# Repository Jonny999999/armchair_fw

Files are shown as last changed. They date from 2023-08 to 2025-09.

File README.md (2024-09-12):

# Overview
This repository contains the firmware for a custom-built automated electric armchair.  
Detailed project information and documentation is available on the website:
- ~~V1: [Electric Armchair V1](https://pfusch.zone/electric-armchair)~~
- V2: [Electric Armchair V2](https://pfusch.zone/electric-armchair-v2)

**Note:** In the current version _V2.2_, only the esp-project in the [board_single/](board_single) folder and the custom libraries in [common/](common) are used.  
The projects in the folders `board_control/` and `board_motorctl/` are no longer compatible and are legacy from _V2.1_.

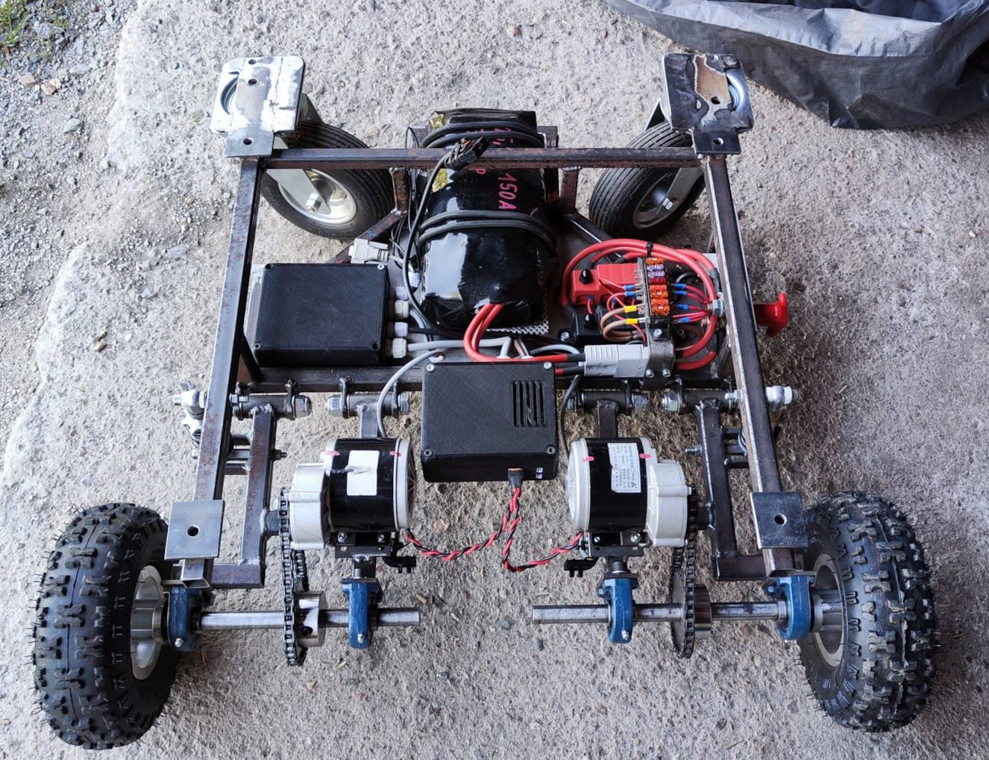
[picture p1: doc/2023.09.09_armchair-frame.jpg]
Photo machine
<br>
*Photo of the built frame that carries the armchair*

<br>

## Current Features
- **Control Modes:**
  - **Joystick:** Control movement via hardware joystick mounted on the right armrest
  - **HTTP:** Control movement via virtual joystick on a web interface
  - **Massage:** Armchair shaking depending on stick position
  - **Adjust:** Control leg and backrest position via joystick
  - **Auto:** Execute stored driving commands sequentially
- **Advanced Motor Control:**
  - Deceleration limit
  - Acceleration limit
  - Current limit
  - Braking
  - Compatible with different motor drivers:
    - 3 pins: A, B, PWM - e.g. various common H-Bridges
    - 1 pin: UART/RS232 - e.g. Sabertooth
- **Input/Sensors:**
  - **Speed Measurement:** Measures speed and direction of each tire individually using custom built encoders
  - **Current Measurement:** Monitors current of each motor
  - **Battery Voltage:** Measures battery voltage and calculates percentage according to discharge curve
  - **Analog Joystick:** 
    - Evaluate two analog signals to get coordinates, radius and angle
    - Calibration wizard/sequence
    - Calibration stored persistently in nvs
- **Fan Control:** Cooling fan for motor driver are activated when needed only
- **Buzzer:** Provides acoustic feedback when switching modes or interacting with menu
- **OLED-Display + Rotary-encoder:**
  - Various status screens showing battery status, speed, RPM, motor current, mode, power, duty cycle, stick data
  - Menu for setting various options using encoder
  - Changed settings are stored persistently in NVS flash
  - Menu for selecting the control mode
- **UART Communication between 2 Boards (V2.1)**
- **Electric Chair Adjustment:** Control 4 Relays powering motors that adjust the chair rest positions
- **Wi-Fi:**
  - Hosts wireless network
  - Web server with webroot in SPIFFS
  - HTTP API for controlling the chair (remote control)
- **React web-app:** Virtual joystick sending data to http-API (placed in SPIFFS)

## Planned Features
#### Hardware
- More Sensors:
  - Accelerometer
  - Lidar sensor / collision detection
  - GPS receiver
  - Temperature sensors
- Lights
- Camera
#### Algorithms
- Anti-Slip Regulation
- Self-Driving Algorithm
#### UI
- Improved Web Interface
  - Settings
  - Chair adjustment
- Simple App

<br>

## Hardware Setup / Electrical
### Control-PCB
The firmware is designed for an ESP32 microcontroller integrated into a custom PCB developed here: [Project Work 2020](https://pfusch.zone/project-work-2020)

### Connection Plan
A detailed diagram illustrating all components and wiring can be found in the file [connection-plan.drawio.pdf](connection-plan.drawio.pdf).   
For more details refer to the documentation on the [website](https://pfusch.zone/electric-armchair-v2).

### Chair-Adjust Relay-Board
A custom pcb with relays and protection for controlling the 2 motors that adjust the rest positions of the armchair was created in this repository as well:
Date: 2024.09.08  
Folder: [hardware/chairAdjust-relayBoard](hardware/chairAdjust-relayBoard)  
Schematic: [hardware/chairAdjust-relayBoard/export/schematic.pdf](hardware/chairAdjust-relayBoard/export/schematic.pdf)
<br>
<br>
<p align="center">

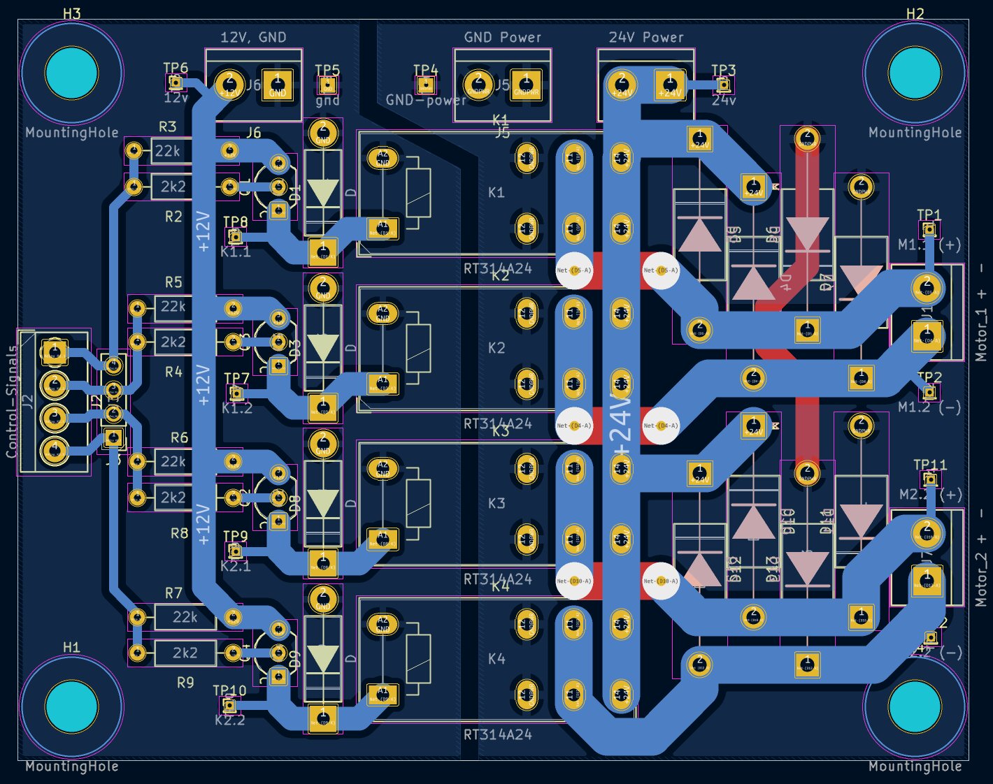
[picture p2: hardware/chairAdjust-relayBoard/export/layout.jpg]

</p>

<br>
<br>

# Installation
### Install ESP-IDF
For this project **ESP-IDF v4.4.4** is required
```bash
#download esp-idf
yay -S esp-idf #alternatively clone the esp-idf repository from github
#run installation script in installed folder
/opt/esp-idf/install.sh
```
### Clone Repository
```
git clone git@github.com:Jonny999999/armchair_fw
```
### Install Node Packages
Navigate to the react-app directory and install required packages using npm:
```
cd react-app
npm install
```

<br>
<br>

# Building the Project
## React-webapp
When flashing to the ESP32, the files in the `react-app/build/` folder are written to a SPIFFS partition.  
These files are then served via HTTP in the Wi-Fi network "armchair" created by the ESP32.  

Initially, or when changing the React code, you need to manually build the React app:
```bash
cd react-app
#compile
npm run build
#remove unwanted license file (filename too long for spiffs)
rm build/static/js/main.8f9aec76.js.LICENSE.txt
```
**Note:** For testing the app locally, use `npm start`

## Firmware
### Environment Setup
```bash
source /opt/esp-idf/export.sh
```
Run once per terminal

### Compilation
```bash
cd board_single
idf.py build
```

### Upload
- Connect FTDI programmer to board (GND to GND, TX to RX, RX to TX)
- Press RESET and BOOT button
- Release RESET button (keep pressing boot)
- Release boot button
- Run flash command:
```bash
idf.py flash
```

### Monitor
To view log output for debugging, follow the same steps as in the Upload section, but run:
```bash
idf.py monitor
```

<br>
<br>

# Usage / User Interface

## Quickstart
- **Browse / select any mode**
  - `[long press]` opens menu for selecting the desired mode (*JOYSTICK* for driving)
- **Driving**
  - `[3x click]` enters *JOYSTICK* mode
- **Rest position**
  - `[rotate]` adjusts the leg rest position  
  - `[press + rotate]` at the same time: adjusts the back rest position
  - alternatively enter *ADJUST* mode and control rests via joystick

<br>

## Encoder Functions
- *When not in MENU mode*, **rotating the encoder** has the following functions:

| Encoder Event | Action |
|---|---|
| rotate left | Move leg rest up by 10% |
| rotate right | Move leg rest DOWN by 10% |
| press + rotate left | Move back rest down by 5% |
| press + rotate left | Move back rest up by 5% |

Note: first tick is ignored -> quickly rotate 2 ticks at first

<br>

- *When not in MENU mode*, **clicking the encoder** has the following functions:

| Count | Type | Action | Description |
|---|---|---|---|
| 1x long | switch mode | **MENU_MODE_SELECT** | Open **menu for selecting the current control mode** |
| 1x | control | [MASSAGE] **freeze** input  | When in massage mode: lock or unlock joystick input at current position. |
| 1x short, 1x long | switch mode | **ADJUST-CHAIR**  | Switch to mode where the armchair leg and backrest are controlled via joystick. |
| 2x | toggle mode | **IDLE** <=> previous| Enable/disable chair armchair (e.g., enable after startup or switch to previous mode after timeout). |
| 3x | switch mode | **JOYSTICK** | Switch to JOYSTICK mode, to control armchair using joystick (default). |
| 4x | switch mode | **HTTP** | Switch to **remote control** via web-app `http://191.168.4.1` in wifi `armchair`. |
| 5x | switch mode | **MENU_SETTINGS** | Open menu to set various options, controlled via display and rotary encoder. |
| 6x | switch mode | **MASSAGE** | Switch to MASSAGE mode where armchair shakes differently, depending on joystick position. |
| 7x | | | |
| 8x | toggle option| **deceleration limit** | Disable/enable deceleration limit (default on) => more responsive. |
| 12x | toggle option| **alt stick mapping** | Toggle between default and alternative stick mapping (reverse direction swapped). |

<br>

- When in **MENU_SETTINGS mode** (5x click), the encoder controls the settings menu: (similar in MENU_MODE_SELECT)

| Encoder Event | Current Menu | Action |
|---|---|---|
| long press | main-menu | Exit MENU mode to previous control mode (e.g., JOYSTICK). |
| long press | value-select | Exit to main-menu without changing the value. |
| click | main-menu | Select currently highlighted menu item -> enter value-select screen. |
| click | value-select | Confirm value / run action. |
| rotate | main-menu | Scroll through menu items. |
| rotate | value-select | Change value. |

<br>

## HTTP Mode
Control the armchair via a virtual joystick on the web interface.

**Usage:**
- Switch to HTTP mode (4 button presses or via mode-select menu).
- Connect to WiFi `armchair`, no password.
- Access http://192.168.4.1 (note: **http** NOT https, some browsers automatically add https!).

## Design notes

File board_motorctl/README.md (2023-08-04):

Firmware for a homemade automated electric armchair.  
More details about this project: https://pfusch.zone/electric-armchair

# Installation
### Install esp-idf
For this project **ESP-IDF v4.4.4** is required (with other versions it might not compile)
```bash
#download esp-idf
yay -S esp-idf #alternatively clone the esp-idf repository from github
#run installation script in installed folder
/opt/esp-idf/install.sh
```
### Clone this repo
```
git clone git@github.com:Jonny999999/armchair_fw
```
### Instal node packages
For the react app packages have to be installed with npm TODO: add this to cmake?
```
cd react-app
npm install
```

# Compilation
## react-webapp
For the webapp to work on the esp32 it has to be built.
When flashing, the folder react-app/build is flashed to siffs (which is used as webroot) onto the esp32.
The following command builds the react webapp and creates this folder
TODO: add this to flash target with cmake?
```bash
cd react-app
#compile
npm run build
#remove unwanted license file (filename too long for spiffs)
rm build/static/js/main.8f9aec76.js.LICENSE.txt
```
Note: Use `npm start` for starting the webapp locally for testing

## esp project
### Set up environment
```bash
source /opt/esp-idf/export.sh
```
(run once in terminal)

### Compile
```bash
idf.py build
```

### Upload
- connect FTDI programmer to board (VCC to VCC; TX to RX; RX to TX)
- press REST and BOOT button
- release RESET button (keep pressing boot)
- run flash command:
```bash
idf.py flash
```
- once "connecting...' successfully, BOOT button can be released

### Monitor
- connect FTDI programmer to board (VCC to VCC; TX to RX; RX to TX)
- press REST and BOOT button
- release RESET button (keep pressing boot)
- run monitor command:
```bash
idf.py monitor
```
- once connected release BOOT button
- press RESET button once for restart

# Hardware setup
## pcb
Used pcb developed in this project: https://pfusch.zone/project-work-2020

## connection plan
A diagram which shows what components are connected to which terminals of the pcb exists here:  
[connection-plan.drawio.pdf](connection-plan.drawio.pdf)

# Planned Features
- More sensors:
  - Accelerometer
  - Lidar sensor
  - GPS receiver
- Anti slip regulation
- Self driving algorithm
- Lights
- drinks holder
- improved webinterface

# Todo
**Add switch functions**
- set loglevel
- define max-speed
- calibrate joystick (min, max, center)
- testing mode / dry-run

# Usage
## Switch functions
**Currently implemented**
| Count | Type | Action | Description |
| --- | --- | --- | --- |
| 1x | configure | [JOYSTICK] **calibrate stick** | when in joystick mode: set joystick center to current joystick pos |
| 1x | control | [MASSAGE] **freeze** input | when in massage mode: lock or unlock joystick input at current position |
| 2x | toggle mode | **IDLE** <=> previous | enable/disable chair armchair e.g. enable after startup or timeout |
| 3x | switch mode | **JOYSTICK** | switch to default mode JOYSTICK |
| 4x | toggle mode | **HTTP** <=> JOYSTICK | switch to '**remote control** via web-app `http://191.168.4.1`' or back to JOYSTICK mode |
| 5x | | | |
| 6x | toggle mode | **MASSAGE** <=> JOYSTICK | switch to MASSAGE mode or back to JOYSTICK mode |
| 7x | | | |
| 8x | toggle option | **deceleration limit** | disable/enable deceleration limit (default on) => more responsive |
| | | | |
| 12x | toggle option | **alt stick mapping** | toggle between default and alternative stick mapping (reverse swapped) |
| >1s | system | **restart** | Restart the controller when pressing the button longer than 1 second | 
| 1x short, 1x long | auto command | **eject** foot support | automatically go forward and reverse for certain time with no acceleration limits, so foot support ejects |

## HTTP mode
Control armchair via virtual joystick on a webinterface.  

**Usage**
- Connect to wifi `armchar`, no password
- Access http://192.168.4.1  (note: **http** NOT https, some browsers automatically add https!)  

**Current Features**
- Control direction and speed with joystick  

**Todo**
- Set parameters
- Control other modes
- Execute preset movement commands

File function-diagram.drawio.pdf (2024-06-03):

# joystick mapping

## Turn right

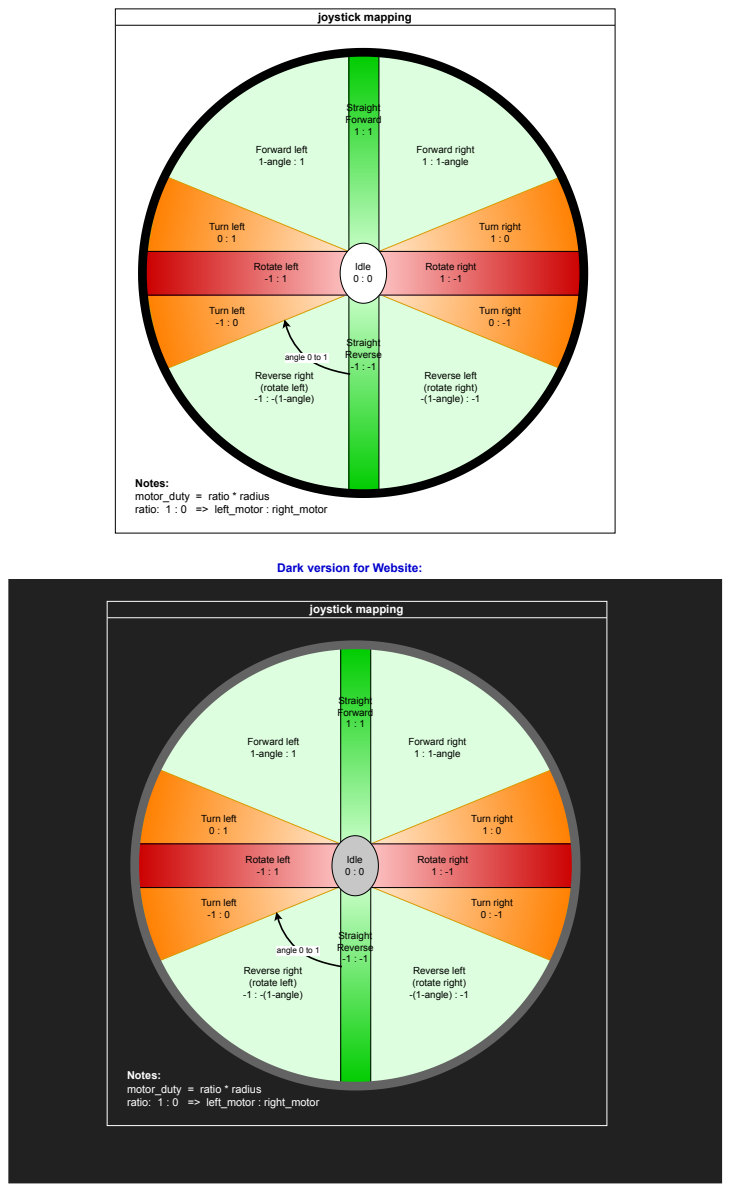
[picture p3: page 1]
Turn left 0 : 1; Rotate left -1 : 1; Rotate right 1 : -1; Straight Reverse -1 : -1; Straight Forward 1 : 1; Forward left 1-angle : 1; Forward right 1 : 1-angle; Reverse right (rotate left) -1 : -(1-angle); Reverse left (rotate right) -(1-angle) : -1; angle 0 to 1; Turn right 0 : -1; Turn left -1 : 0; Idle 0 : 0; Notes: motor_duty = ratio * radius ratio: 1 : 0 => left_motor : right_motor; joystick mapping; Turn right 1 : 0

Dark version for Website:

UART board communication (V2.1)

MOTOR COMMANDS
[ interval, fast ]

timestamp
motorcommands
- motorCommand_t left
- motorstate
- duty

CONFIG
[ manual / on change ]

timestamp
motorctl_config_t
- msFadeAccel
- msFadeDecel
- bool currentLimitEnabled
- (currentSensor_adc)
(currentSensor_ratedCurrent)
- currentMax
- deadTimeMs

board control

- joystick
- encoder, switch
- display

board motorctl

- 2x driver
- 2x currentsensor
- 2x light barrier axle speed
- 2x brake resistor
- temp sensors
- motor
- driver
- brake resistor
- fan

MOTORCTL_STATUS
[ interval, slow ]

timestamp
motorcommands (current actual duty, direction) motor currents
axle rotating speed
temperatures
- motors
- drivers
- brake resistors
fan target state [ ] handled by motorctl board battery voltage
config?

## UART

Planning data / structs
need to be sent between the two boards here:

NOTE: the below diagrams are significantly outdated -- needs update to match the actual code again

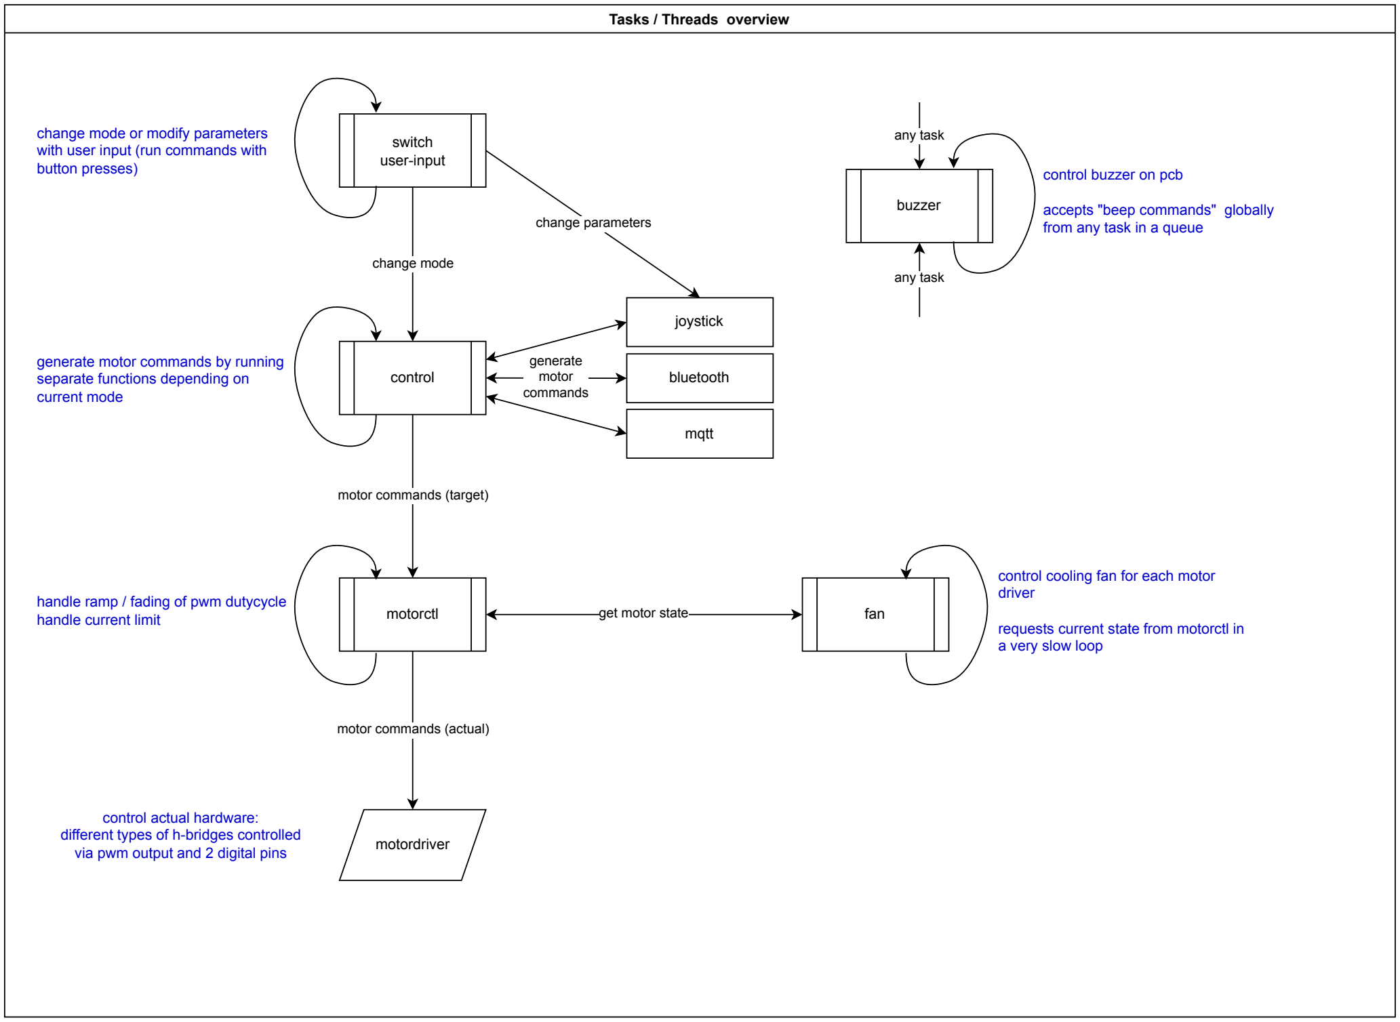
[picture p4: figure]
Tasks / Threads overview; motordriver; joystick; motor commands (actual); motorctl; switch user-input; motor commands (target); control; bluetooth; control actual hardware: different types of h-bridges controlled via pwm output and 2 digital pins; handle ramp / fading of pwm dutycycle handle current limit; generate motor commands by running separate functions depending on current mode; change mode or modify parameters with user input (run commands with button presses); change mode; generate motor commands; mqtt; get motor state; fan; control cooling fan for each motor driver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
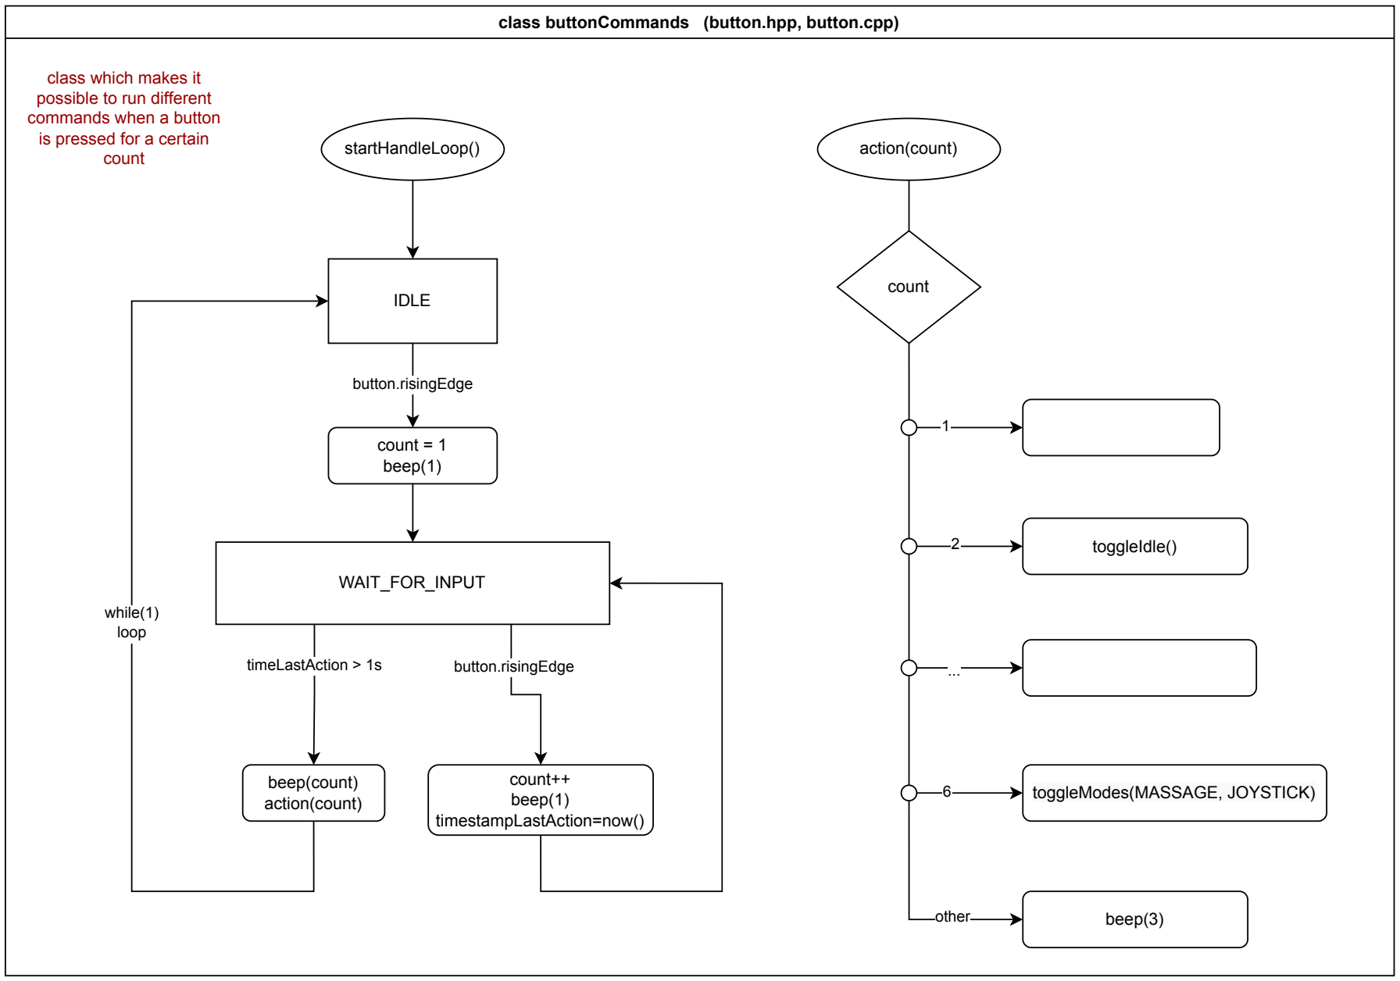
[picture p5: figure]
class buttonCommands (button.hpp, button.cpp); WAIT_FOR_INPUT; count++ beep(1) timestampLastAction=now(); button.risingEdge; IDLE; count = 1 beep(1); count; toggleIdle(); while(1) loop; beep(count) action(count); timeLastAction > 1s; beep(3); toggleModes(MASSAGE, JOYSTICK); other; startHandleLoop(); action(count); class which makes it possible to run different commands when a button is pressed for a certain count

class controledArmchair (control.hpp, control.cpp)

mode:
JOYSTICK

mode:
MQTT

mode:
IDLE

commands =
joystick_generateCmdsDrive(joystick) | while(1) loop

motorLeft.setTarget(command.left.state, command.left.duty) motorRight.setTarget(command.right.state, command.right.duty) commands.right = {IDLE, 0}
commands.left = {IDLE, 0} | Queue_receive (mqttQueue, &command)

changeMode(modeNew)

mode

startHandleLoopl()

MQTT
timeout?

mode:
MASSAGE

commands =
joystick_generateCmdsMassage(joystick)

mode:
BLUETOOTH?

mode:
AUTO?

generate motor
commands by calling
functions
corresponding to
current mode

send target state and duty to controlledMotor object of each motor (controlledMotor applies ramp and current limit and commands motor driver repeatedly)

TODO: timeout
switch to idle when no
change over long time

TODO: add option
"debug / disable motors / dry-run": run the functions to generate the commands and outputs them, but do not send to motor control

run functions corresponding to the current mode that generate motor commands,

send the resulting commands to motorctl

mode = modeNew;

toggleIdle() | toggleModes(modePrimary, modeSecondary)
mode | IDLE | mode = modePrevious

modePrevious = mode
mode = IDLE

[other]

mode | modePrimary | mode = modeSecondary

mode = modePrimary

[other]

toggle between IDLE and
previous or default mode switch to specific mode toggle between two specific modes e.g. button press switches between MASSAGE and JOYSTICK

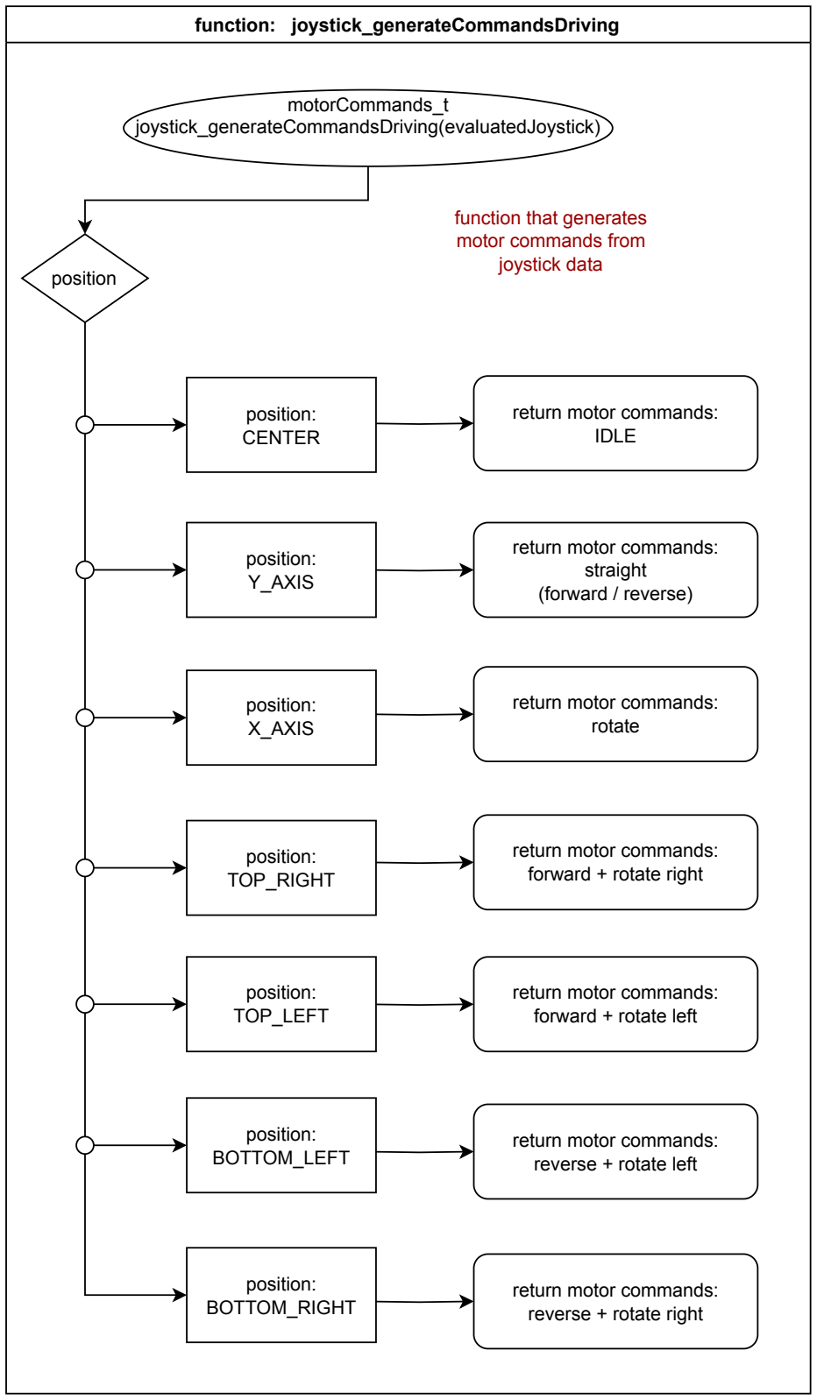
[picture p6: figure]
function: joystick_generateCommandsDriving; motorCommands_t joystick_generateCommandsDriving(evaluatedJoystick); return motor commands: IDLE; return motor commands: straight (forward / reverse); return motor commands: rotate; return motor commands: forward + rotate right; return motor commands: forward + rotate left; return motor commands: reverse + rotate left; return motor commands: reverse + rotate right; position: CENTER; position: Y_AXIS; position: X_AXIS; position: TOP_RIGHT; position: TOP_LEFT; position: BOTTOM_LEFT; position: BOTTOM_RIGHT; position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

class evaluatedJoystick (joystick.hpp, joystick.cpp)

defineCenter()

float getCooridnate(gpio, min, max, center, tolerance)

voltage
> max - tolerance

voltage
< min + tolerance

else

else

voltage < center +
tolerance
&& voltage > center -
tolerance

return 0

return 1

return -1

center

max

min

voltage
> center

else

voltage
< center

else

positive area
(above center)

negative area
(below center)

range = max - center - 2* tolerance return (voltage - center - tolerance) / range

range = center - min - 2* tolerance return - (center - voltage - tolerance) / range x = getCoordinates (gpio_x, min, max, center, tolerance) y = getCoordinates (gpio_y, min, max, center, tolerance)

voltage = read_adc(gpio)

radius = sqrt(pow(joystick.x,2) + pow(joystick.y,2));

angle = (atan(joystick.y/joystick.x) * 180) / 3.141

struct getData()

define state "position" enum
[ CENTER, Y_AXIS, X_AXIS, TOP_RIGHT, TOP_LEFT, BOTTOM_LEFT, BOTTOM_RIGHT ]

x_center = read_adc(gpio_x) y_center = read_adc(gpio_y)

return data struct:
joystickData_t {
joystickPos_t position;
float x;
float y;
float radius;
float angle;
}

function that makes it
possible to get a struct
with current state and
data of the joystick.

this can be used as
input in other functions
or tasks

private function that
reads an analog input
and calculates
coodrinates according
to given parameters

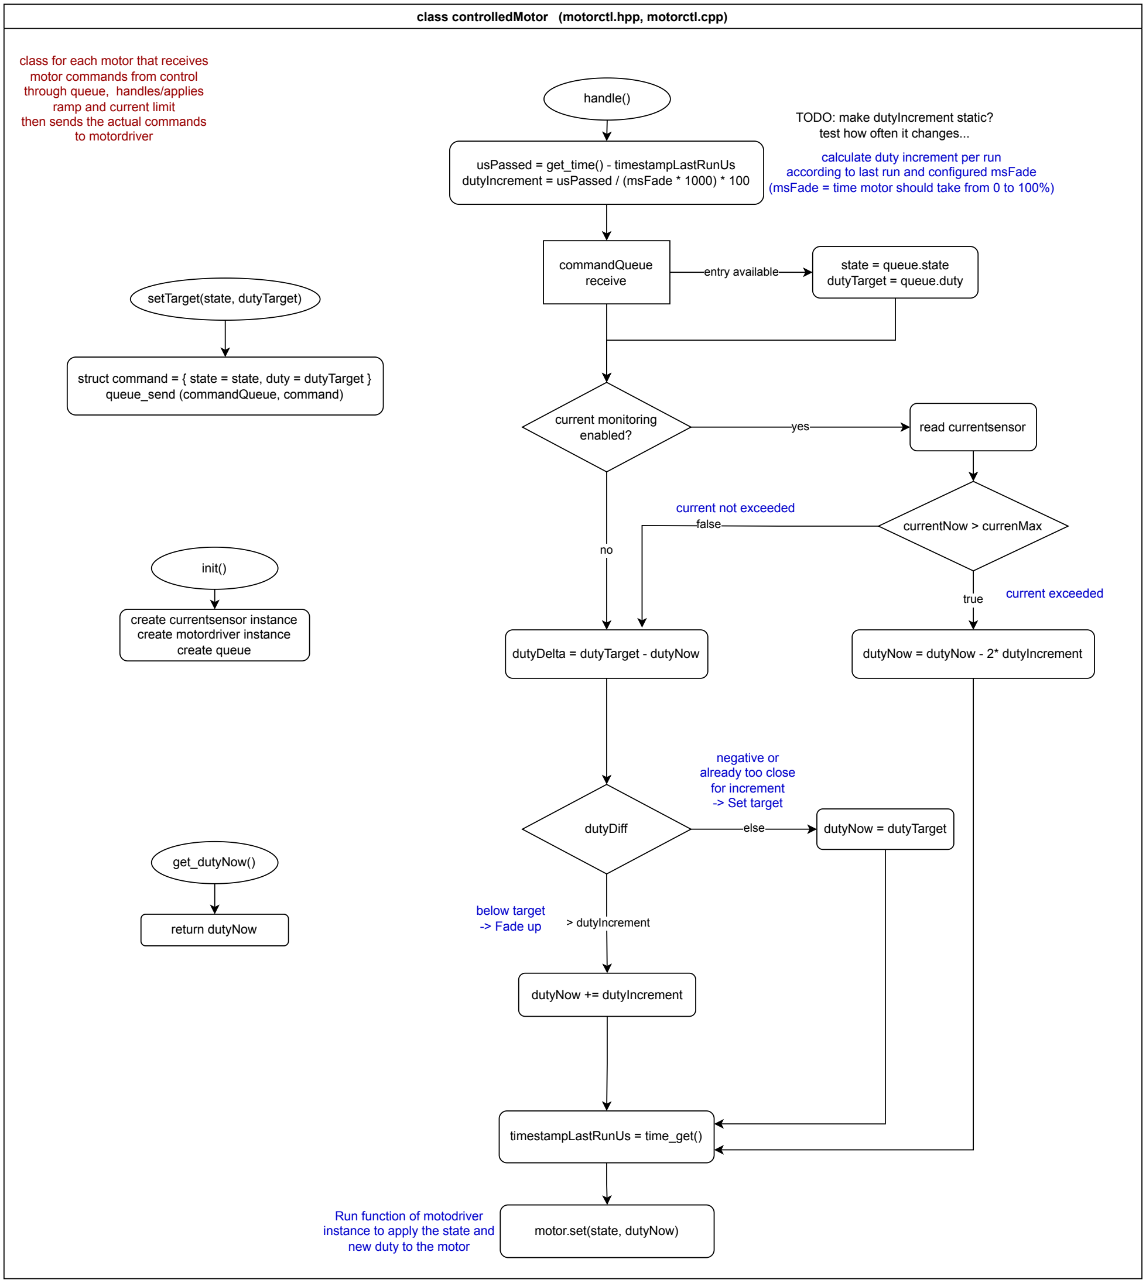
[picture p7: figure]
class controlledMotor (motorctl.hpp, motorctl.cpp); init(); create currentsensor instance create motordriver instance create queue; handle(); state = queue.state dutyTarget = queue.duty; entry available commandQueue receive; read currentsensor; > dutyIncrement; dutyDiff; else; dutyNow += dutyIncrement; dutyNow = dutyTarget; dutyDelta = dutyTarget - dutyNow; yes; current monitoring enabled?; true; currentNow > currenMax; dutyNow = dutyNow - 2* dutyIncrement; timestampLastRunUs = time_get(); false; current not exceeded; current exceeded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

struct command = { state = state, duty = dutyTarget } dutyIncrement = usPassed / (msFade * 1000) * 100 according to last run and configured msFade (msFade = time motor should take from 0 to 100%)

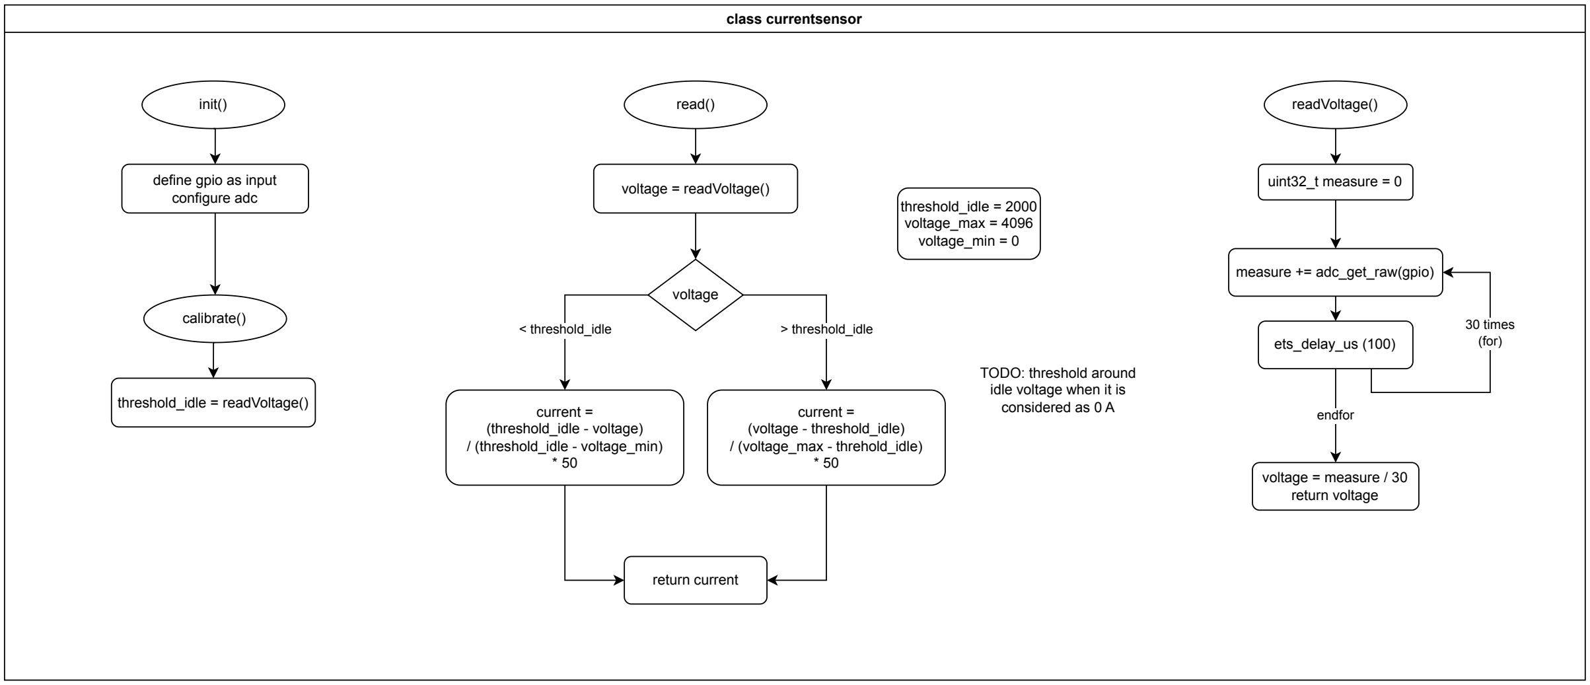
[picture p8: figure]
class currentsensor; init(); define gpio as input configure adc; read(); calibrate(); readVoltage(); threshold_idle = readVoltage(); voltage = readVoltage(); < threshold_idle; > threshold_idle; voltage; current = (voltage - threshold_idle) / (voltage_max - threhold_idle) * 50; current = (threshold_idle - voltage) / (threshold_idle - voltage_min) * 50; threshold_idle = 2000 voltage_max = 4096 voltage_min = 0; return current; TODO: threshold around idle voltage when it is considered as 0 A; measure += adc_get_raw(gpio); 30 times (for); endfor; ets_delay_us (100)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

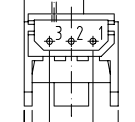
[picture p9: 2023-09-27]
doc/tcsy5201-pinout.png

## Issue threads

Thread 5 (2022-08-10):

Fix bug where armchair drives unexpectedly when switching from MASSAGE to STICK (needs testing)

Jonny999999, 2022-08-10:
Noticed a few times that armchair started driving forward for some time (2-3s) with no user input / no way to stop
after switching from massage to joystick mode
--> test and fix this

Jonny999999, 2024-03-17:
Probably will be fixed in https://github.com/Jonny999999/armchair_fw/issues/6

Jonny999999, 2024-06-19:
fixed for now in c738ac96b1e244f432a9adc716c1c16700d41160

Closed 2024-06-19.

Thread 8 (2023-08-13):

Add  CURRENT SENSOR  support

Jonny999999, 2023-08-13:
as in old firmware project add support for limiting current, hardware already implemented

- [x] configure current sensors
- [x] test whether current sensors work
- [x] read current sensors
- [x] handle limit
- [ ] set limit (config/command?)

Jonny999999, 2024-06-19:
added currentsensor support in a6de6c4c109d7c861714625bb8987b024031452a already.
current limit implemented but not really used, since using new over-current safe motor driver hardware.
Currently only used for monitoring in status display

Closed 2024-06-19.

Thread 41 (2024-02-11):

Optimize chair-adjustment (leg and back rest)

Jonny999999, 2024-02-11:
ideas and todo's for improving the chair adjustment are collected here.
Also see noted todo's in chairAdjust.cpp

## ideas, todo
- [x] add separate task that controls chair adjustment
    - [x] timeout
    - [x] track position
    - [x] re-calibrate automatically ( detect situation when probably at limit )
    - [x] auto-adjust: move to position while driving
    - [ ] control via app
- [x] add delay between direction change (to prevent abuse)

Jonny999999, 2024-09-08:
Added all ideas except the app in the following merge: 6a2efb443293ae4d40704f80b031ac4274f341fa

Closed 2024-09-08.

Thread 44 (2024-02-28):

Unexpected movement when in joystick center

Jonny999999, 2024-02-28:
## Issue
While testing V2.2.1 Idling in joystick mode seems unreliable...
Noticed Armchair randomly starting to move without touching the stick several times.
Even though i just calibrated it a few seconds ago.

Already observed that kind of random action for a few seconds while testing, when putting down the stick on the bench.

## debugging
- find out how to reproduce
- issue with joystick input?
- issue with motorctl task?

Jonny999999, 2024-03-17:
Fixed unreliable connection between ground wires in UI-arm (soldered instead of WAGO).
The issue never occurred again since then.

Closed 2024-03-17.

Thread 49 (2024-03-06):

Leg-support moves during startup or while flashing firmware

Jonny999999, 2024-03-06:
Currently one mosfet controlling a relay for chair-adjust is on by default on startup or flashing until the chair-adjust is initialized. (GPIO15)
- [ ] Find out reason
- [ ] Burn eFuse to permanently disable the feature causing this?
- [ ] alternatively workaround: change pin assignment, so back rest moves up instead of leg rest down, which is less annoying

strapping pin
https://esp32.com/viewtopic.php?t=297
https://electronics.stackexchange.com/questions/622750/esp32-boot-strapping-pins-problem-gpio15-and-gpio5

Jonny999999, 2024-09-08:
Not possible to disable the high on boot behavior due to GPIO 15 being strapping pin on esp32.

Rewiring would be easily possible even without de-attaching the chair.
But it moving down is actually a feature now, since tracking the position time based in 6a2efb443293ae4d40704f80b031ac4274f341fa

Closed 2024-09-08.

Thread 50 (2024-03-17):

Bugged joystick scaling / fast accel - when switching from massage-mode

Jonny999999, 2024-03-17:
Needs testing, certainly is difficult to make precise movements after some time (probably massage mode?).

## current workaround:
reset to defaults (tested)
or restart armchair?

Jonny999999, 2024-06-19:
similar to https://github.com/Jonny999999/armchair_fw/issues/51
fixed

Closed 2024-06-19.

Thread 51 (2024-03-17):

Bugged massage mode - extreme jumps

Jonny999999, 2024-03-17:
Massage mode is currently unusable and even unsafe, due to unexpected long and fast movement
no longer compatible with reworked motorctl task?
needs testing
Note: massage mode needs rework overall, see https://github.com/Jonny999999/armchair_fw/issues/6

Jonny999999, 2024-05-29:
just noticed during testing:
massage mode messes up configuration
accel and decel gets overwritten with way to low 50 ms at change to MASSAGE (even writes to nvs) and not restored after change from MASSAGE

Jonny999999, 2024-06-19:
c738ac96b1e244f432a9adc716c1c16700d41160
store and restore previous configuration when changing to/from MASSAGE mode

Closed 2024-06-19.

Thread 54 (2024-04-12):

UI: Select mode visually using Display+Encoder

Jonny999999, 2024-04-12:
It might be difficult to remember and repeatedly explain the button sequences for changing mode.
=> Add a way to select mode with rotating the encoder until the display shows the desired one

Jonny999999, 2024-06-19:
added mode select menu in 0695c924187e4bfff2c4ac4efdf75155827dbc9e

Closed 2024-06-19.

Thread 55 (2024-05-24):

Move brake detection from 'motorctl' to 'stick-command-generation'?

Jonny999999, 2024-05-24:
Added brake feature (when joystick in opposite direction than currently driving) in f94630711be6c315192846182bf6d5d6d97fc8cd
it works for now but might result in weird behavior in certain conditions

## issue
e.g. brake might trigger on one tire only when switching from full-rot to forward (especially dead time could be confusing)

Maybe move this feature from motorctl task  to joystick command generation?
since detection of braking state is handled for each motor individually now, shouldnt both motors always brake  at the same time?

## tasks
- motorctl:
  - make use of BRAKE motor state
- joystick:
  - detect brake condition from joystick input and motor status

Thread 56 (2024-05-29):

Menu randomly immediately exits when opened

Jonny999999, 2024-05-29:
Bug introduced since c58c6b9b35c843cf89df4522e917954c8838dce8 :

especially when opening the menu with 5x button press it opens for 1 second and closes again
when opening it via the mode select menu there are less issues

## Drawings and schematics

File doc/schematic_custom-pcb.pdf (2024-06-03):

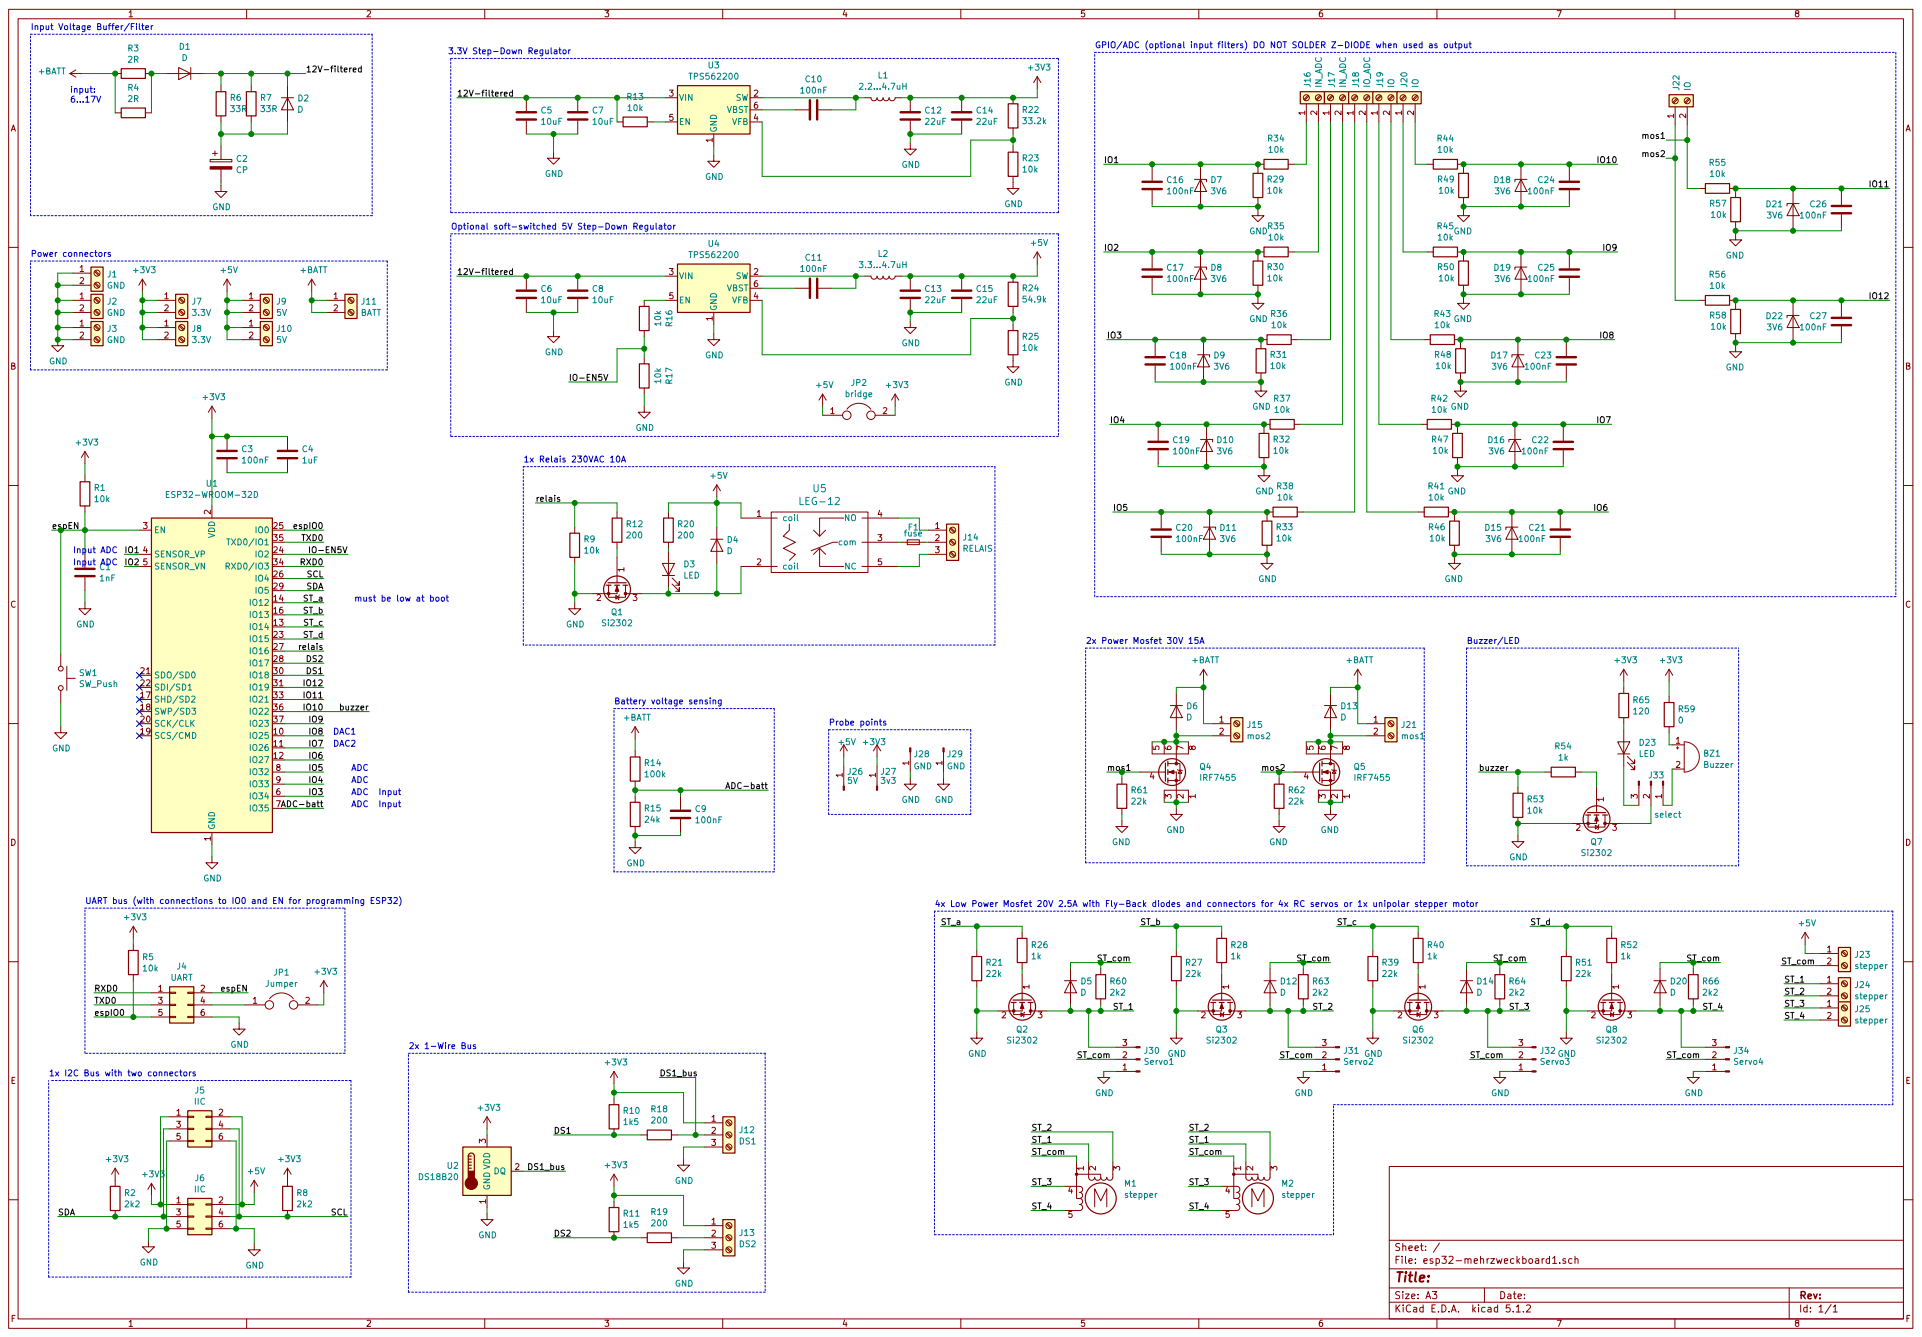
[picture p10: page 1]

1 SW 2 VIN 3 VFB 4 EN 5 VBST 6 U3 TPS562200 L1

1 SW 2 VIN 3 VFB 4 EN 5 VBST 6 U4 TPS562200 L2

2 SCK/CLK 20 SDO/SD0 21 SDI/SD1 22

SCL RXD0 TXD0
relais DS1 DS2 ADC-batt ST_a ST_b ST_c ST_d SDA

Id: 1/1 Title: File: esp32-mehrzweckboard1.sch Sheet: / GND

4x Low Power Mosfet 20V 2.5A with Fly-Back diodes and connectors for 4x RC servos or 1x unipolar stepper motor 2x 1-Wire Bus UART bus (with connections to IO0 and EN for programming ESP32) 1x I2C Bus with two connectors

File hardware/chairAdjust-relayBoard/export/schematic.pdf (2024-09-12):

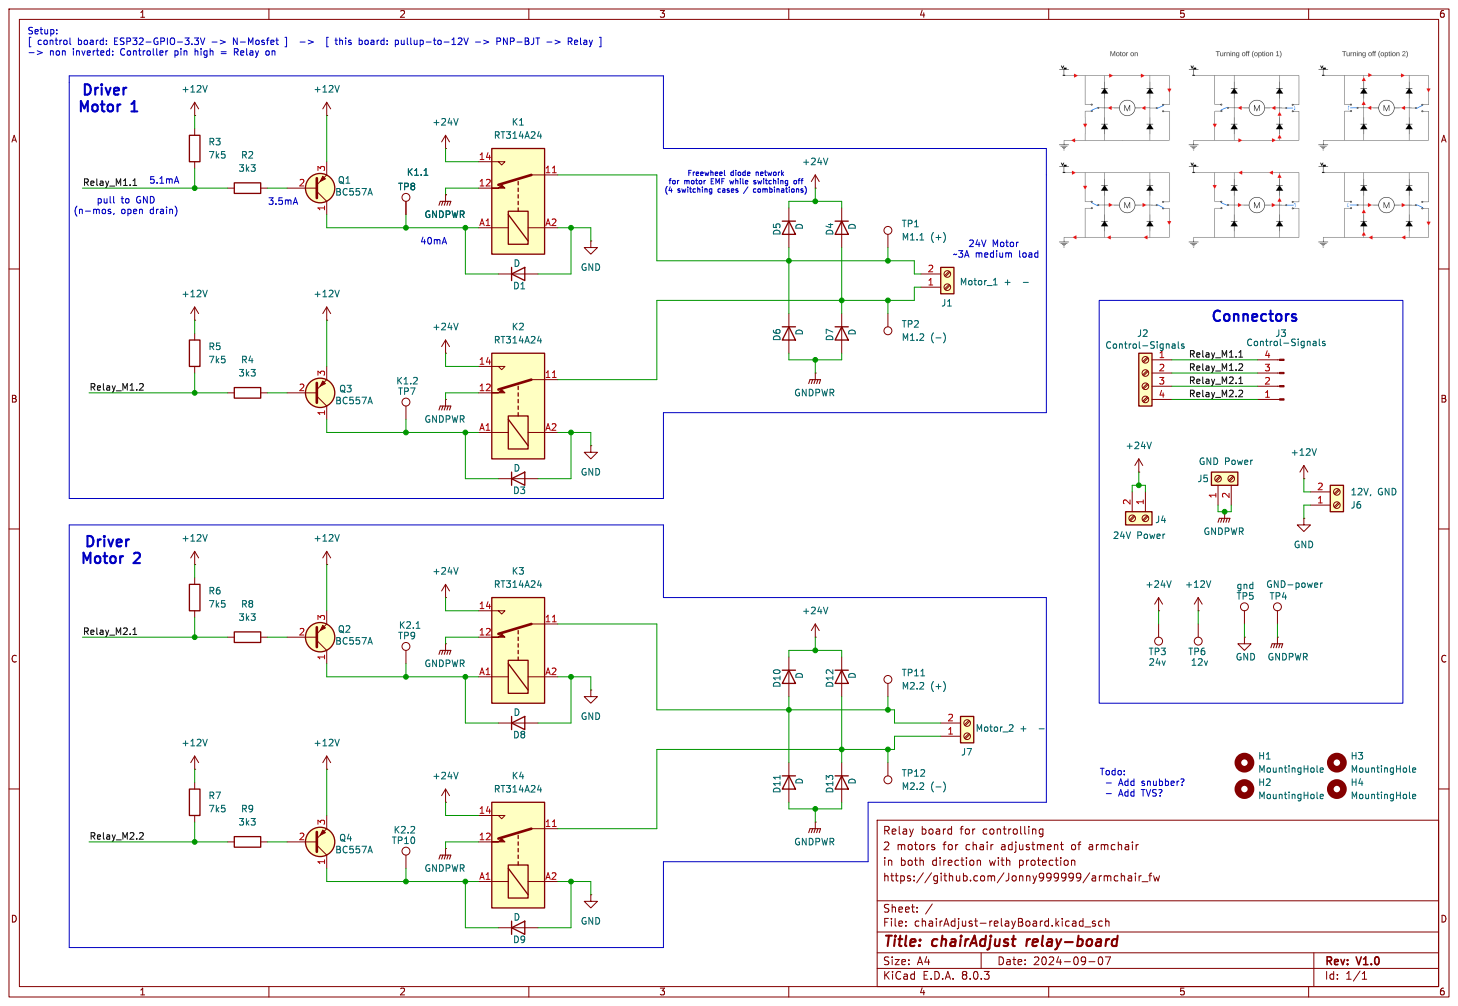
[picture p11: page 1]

File: chairAdjust-relayBoard.kicad_sch Sheet: / https://github.com/Jonny999999/armchair_fw

Id: 1/1 Title: chairAdjust relay-board

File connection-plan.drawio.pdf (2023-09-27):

## 12V from stepdown/fuse GND from stepdown

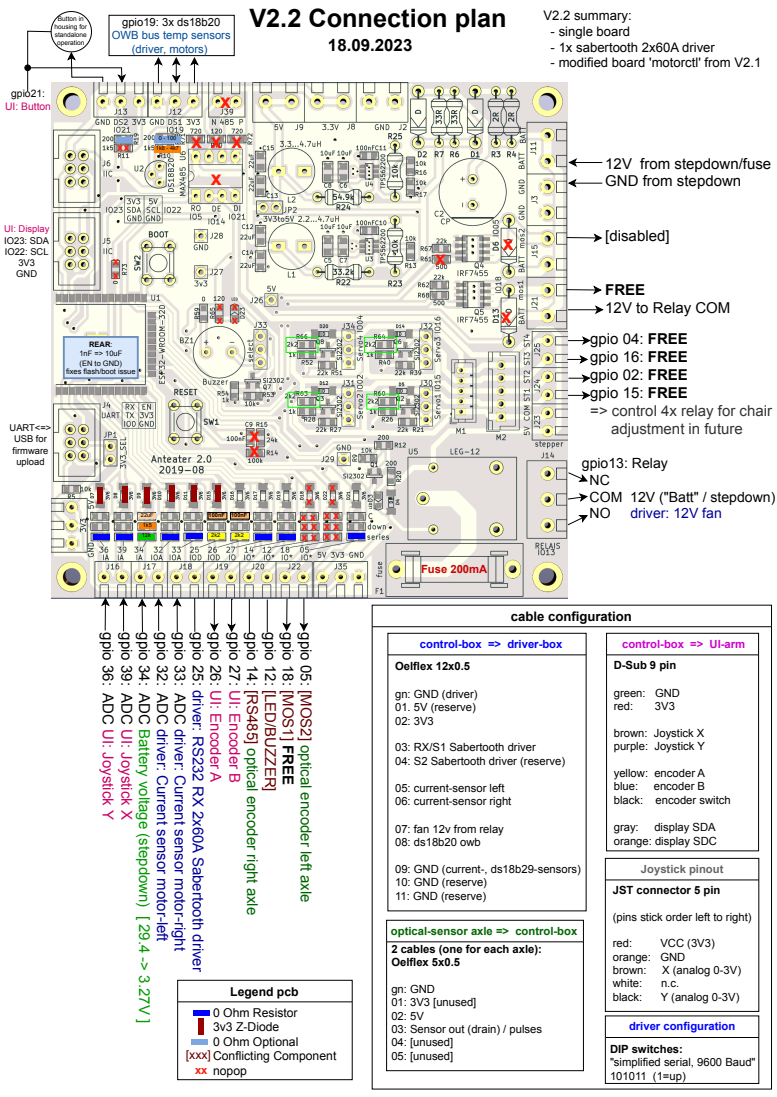
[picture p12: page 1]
gpio 18: [MOS1] FREE; Legend pcb; 0 Ohm Resistor 3v3 Z-Diode 0 Ohm Optional Conflicting Component nopop; [xxx] xx; [disabled]; driver: 12V fan; gpio21: UI: Button; Fuse 200mA; cable configuration; gn: GND (driver) 01. 5V (reserve) 02: 3V3; green: GND; red:; brown: Joystick X purple: Joystick Y; blue:; encoder B; gray:; display SDA; VCC (3V3); orange: GND; brown:; X (analog 0-3V); white:; black:; Y (analog 0-3V); V2.2 Connection plan; V2.2 summary:; UI: Display IO23: SDA IO22: SCL 3V3 GND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

gpio19: 3x ds18b20
OWB bus temp sensors
(driver, motors)

- single board
- 1x sabertooth 2x60A driver
- modified board 'motorctl' from V2.1

FREE
12V to Relay COM
gpio 04: FREE
gpio 16: FREE
gpio 02: FREE
gpio 15: FREE
=> control 4x relay for chair
adjustment in future

REAR:
(EN to GND)
fixes flash/boot issue

gpio13: Relay
COM 12V ("Batt" / stepdown)

gpio 36: ADC UI: Joystick

gpio 39: ADC UI: Joystick X

gpio 34: ADC Battery voltage (stepdown) [ 29.4 -> 3.27V ]

gpio 32: ADC driver: Current sensor motor-left

gpio 33: ADC driver: Current sensor motor-right

gpio 25: driver: RS232 RX 2x60A Sabertooth driver

gpio 26: UI: Encoder

gpio 27: UI: Encoder B

gpio 14: [RS485] optical encoder right axle

gpio 12: [LED/BUZZER]

gpio 05: [MOS2] optical encoder left axle

control-box => driver-box
Oelflex 12x0.5

control-box => UI-arm
D-Sub 9 pin

03: RX/S1 Sabertooth driver
04: S2 Sabertooth driver (reserve)

yellow: encoder A
black: encoder switch

05: current-sensor left
06: current-sensor right

07: fan 12v from relay
08: ds18b20 owb

orange: display SDC

09: GND (current-, ds18b29-sensors)
10: GND (reserve)
11: GND (reserve)

Joystick pinout
JST connector 5 pin

(pins stick order left to right)

optical-sensor axle => control-box
2 cables (one for each axle):
Oelflex 5x0.5

gn: GND
01: 3V3 [unused]
03: Sensor out (drain) / pulses
04: [unused]
05: [unused]

driver configuration
DIP switches:
"simplified serial, 9600 Baud"

## V2.2 Wiring-plan

18.09.2023

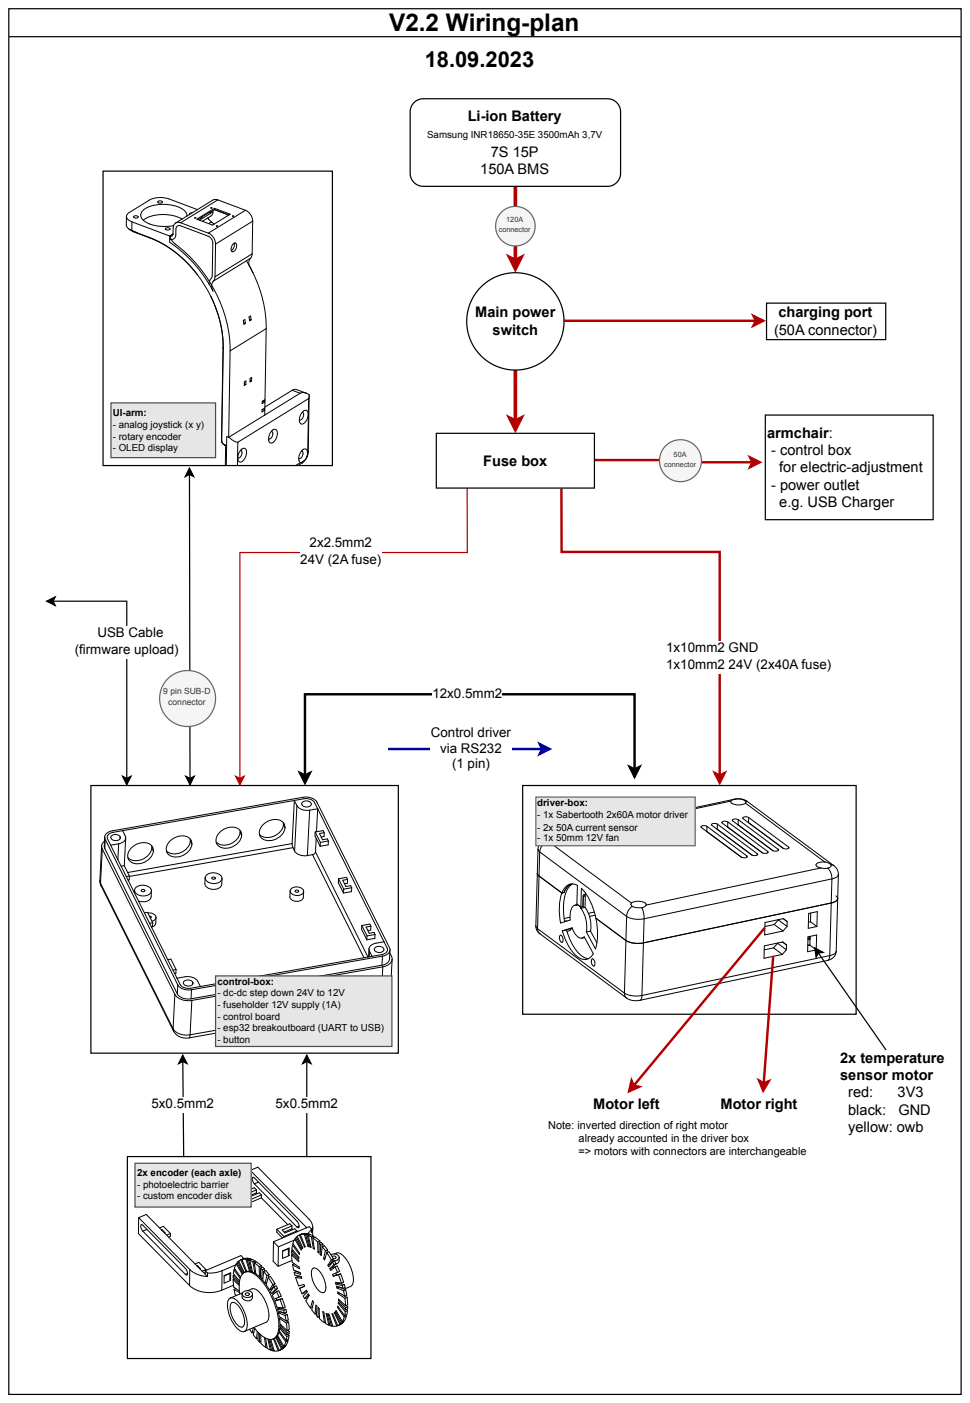
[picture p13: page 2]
USB Cable (firmware upload); 2x2.5mm2 24V (2A fuse); 1x10mm2 GND 1x10mm2 24V (2x40A fuse); 2x temperature sensor motor; red:; black: GND yellow: owb; Motor left; Motor right; UI-arm: - analog joystick (x y) - rotary encoder - OLED display; Fuse box; Main power switch; Samsung INR18650-35E 3500mAh 3,7V 7S 15P 150A BMS; charging port (50A connector); 120A connector; 9 pin SUB-D connector; 50A connector; Control driver via RS232 (1 pin)

Li-ion Battery

armchair:
- control box
for electric-adjustment
- power outlet
e.g. USB Charger

driver-box:
- 1x Sabertooth 2x60A motor driver
- 2x 50A current sensor
- 1x 50mm 12V fan

control-box:
- dc-dc step down 24V to 12V
- fuseholder 12V supply (1A)
- control board
- esp32 breakoutboard (UART to USB)
- button

Note: inverted direction of right motor
already accounted in the driver box
=> motors with connectors are interchangeable

2x encoder (each axle)
- photoelectric barrier
- custom encoder disk

## measure rotational speed + direction

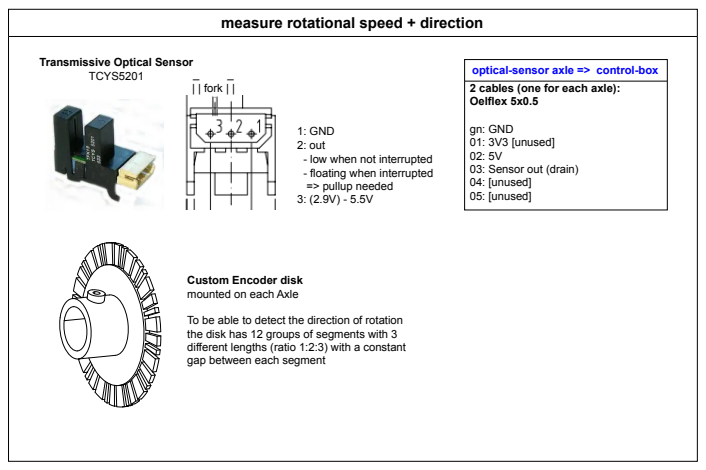
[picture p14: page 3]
| | fork | |; TCYS5201; optical-sensor axle => control-box; gn: GND 01: 3V3 [unused] 02: 5V 03: Sensor out (drain) 04: [unused] 05: [unused]

Transmissive Optical Sensor

2 cables (one for each axle):
Oelflex 5x0.5

1: GND
2: out
- low when not interrupted
- floating when interrupted
=> pullup needed

Custom Encoder disk
mounted on each Axle

To be able to detect the direction of rotation
the disk has 12 groups of segments with 3
different lengths (ratio 1:2:3) with a constant
gap between each segment

# V2.1 Board 1: control

## 12V from pcb motorctl

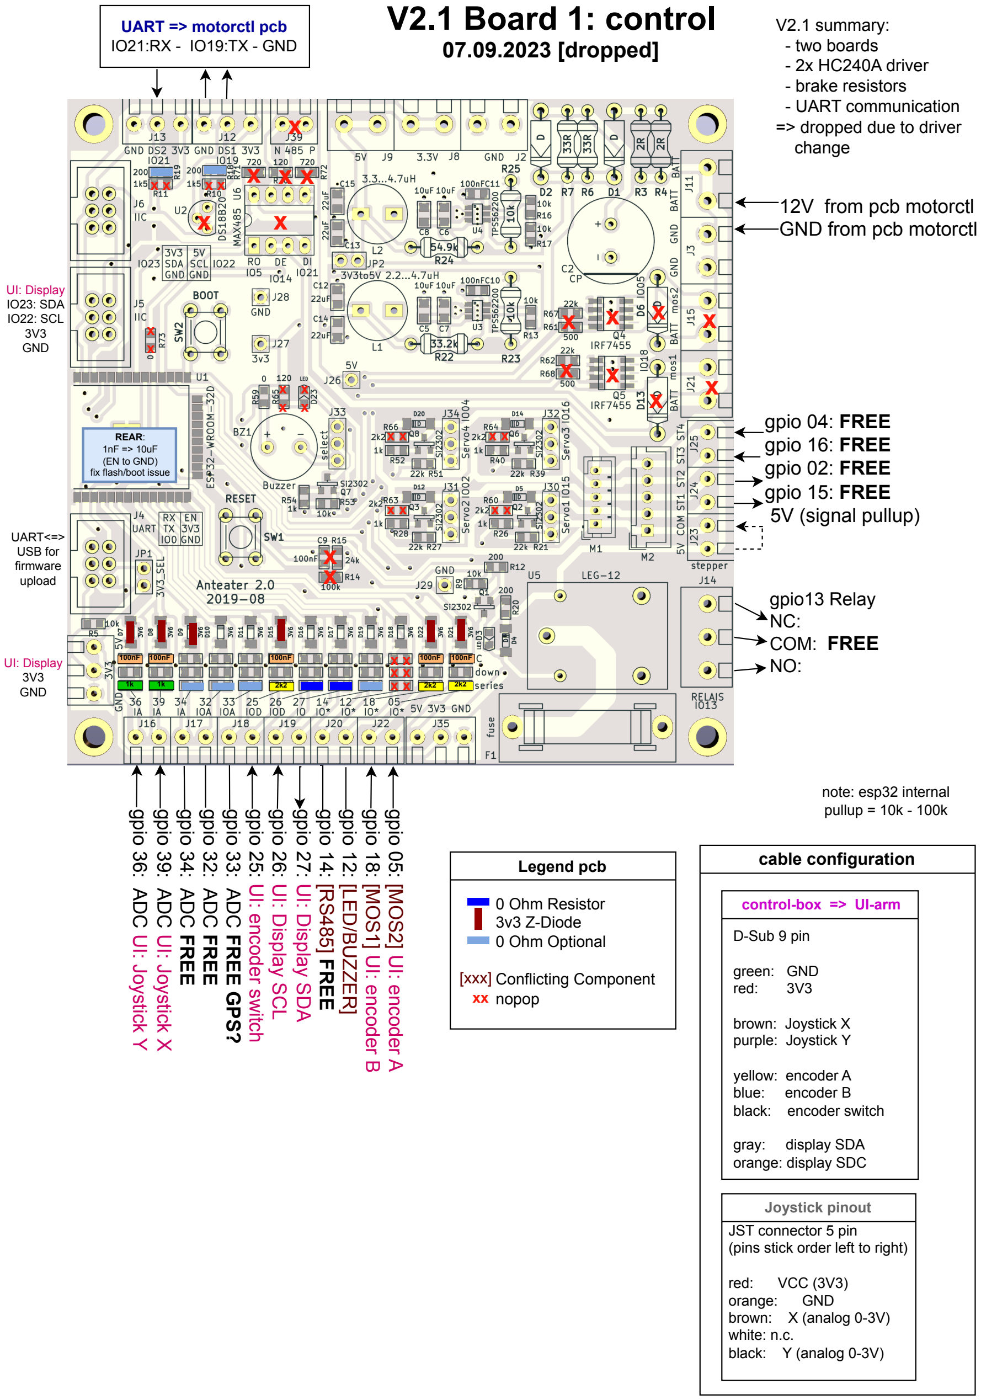
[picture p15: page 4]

## gpio 05: [MOS2] UI: encoder

A

## gpio 18: [MOS1] UI: encoder B

## gpio 12: [LED/BUZZER]

## gpio 14: [RS485] FREE

## gpio 27: UI: Display SDA

## gpio 26: UI: Display SCL

## gpio 25: UI: encoder switch

## gpio 33: ADC FREE GPS?

## gpio 32: ADC FREE

## gpio 34: ADC FREE

## gpio 39: ADC UI: Joystick X

## gpio 36: ADC UI: Joystick

Y

## gpio 04: FREE gpio 16: FREE gpio 02: FREE gpio 15: FREE 5V (signal pullup)

UART => motorctl pcb
IO21:RX - IO19:TX - GND

## GND from pcb motorctl

### gpio13 Relay

NC:
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

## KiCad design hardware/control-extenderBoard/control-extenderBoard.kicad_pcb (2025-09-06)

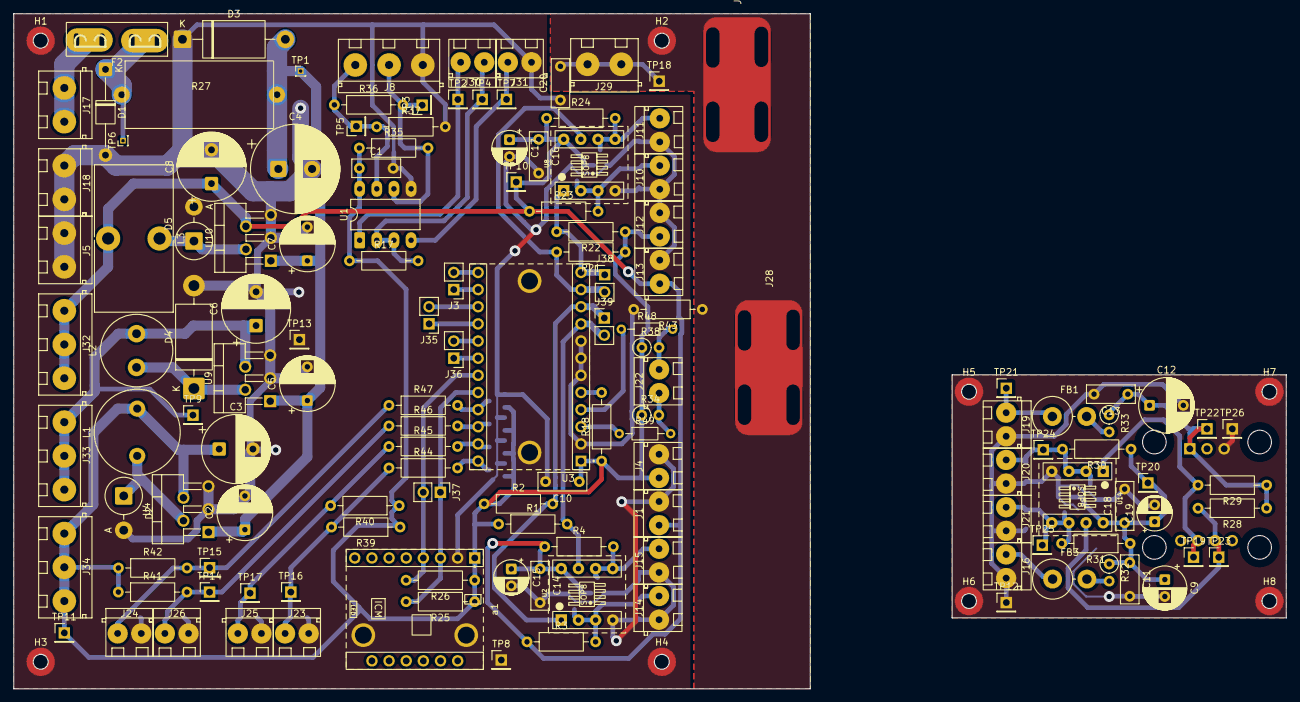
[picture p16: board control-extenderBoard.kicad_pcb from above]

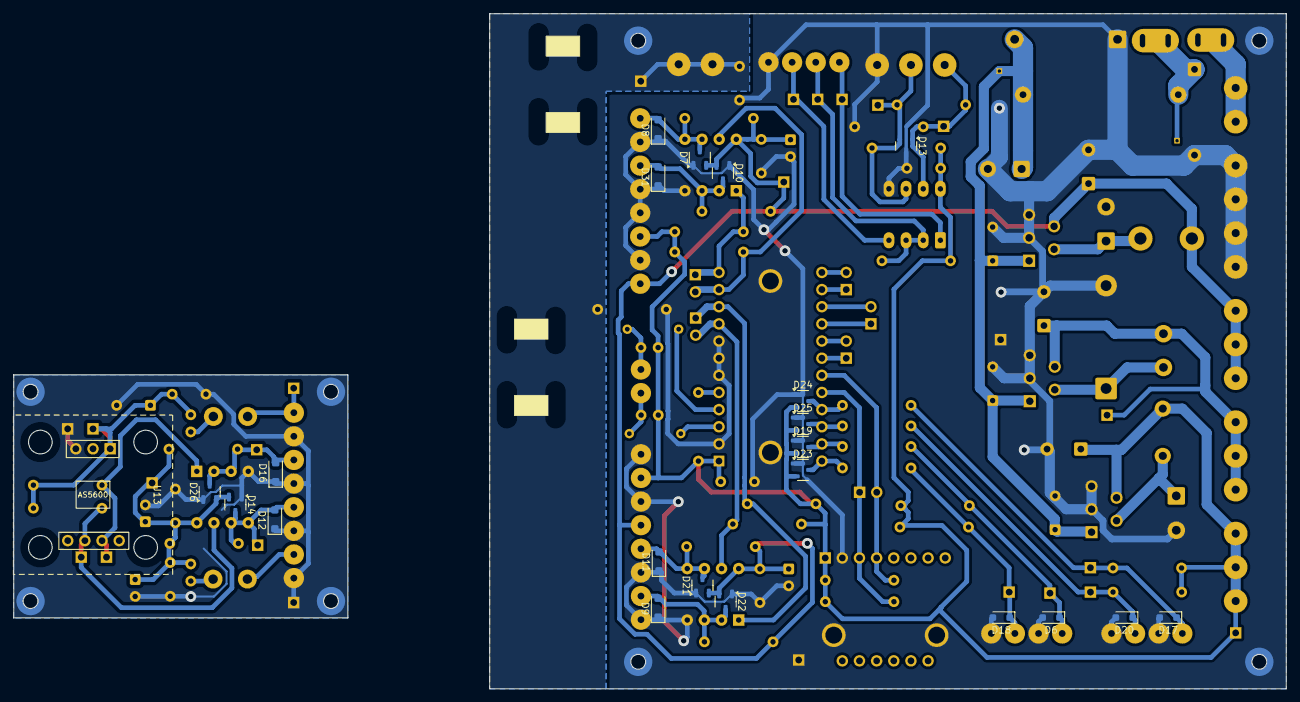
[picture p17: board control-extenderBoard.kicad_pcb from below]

Board: 4 copper layers, 188.5 x 100.0 mm, 166 parts (22 on the bottom side), 56 nets.

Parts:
C1, C10, C11, C13, C14, C16, C18, C20: 100n; C_Disc_D7.0mm_W2.5mm_P5.00mm
C2, C5, C7, C12: 100u; CP_Radial_D8.0mm_P5.00mm
C3, C6, C8: 1000u; CP_Radial_D10.0mm_P5.00mm
C4: 2200uf; CP_Radial_D13.0mm_P5.00mm
C9: 100u; CP_Radial_D6.3mm_P2.50mm
C15, C17, C19: 10uf; CP_Radial_D5.0mm_P2.50mm
D1: D; D_T-1_P12.70mm_Horizontal
D2, D5: 1N5822; D_DO-201AE_P5.08mm_Vertical_AnodeUp
D3: TVS 28V (starts 31V); D_DO-201AE_P15.24mm_Horizontal
D4: 1N5822; D_DO-201AD_P15.24mm_Horizontal
D6, D17, D18, D20: AQ4020-01FTG; D_SOD-323_HandSoldering
D7, D10, D14, D19, D21, D22, D23, D24, D25, D26: BAS70-04; SOT-23-3
D8, D9, D11, D12, D16, D31: PESD12VL1BA; D_SOD-123F
D13: SM712_SOT23; SOT-23
F2: F-total-control-supply; Fuseholder_Automotive-Mini_Fuse11x4x16_Footprint15x5_Inline
FB1, FB3: FerriteBead AWBC-09; R_Axial_DIN0614_L14.3mm_D5.7mm_P5.08mm_Vertical
H1, H2, H3, H4, H5, H6, H7, H8: MountingHole_Pad; MountingHole_2.2mm_NPTH-with-pad_DRC-clearance-error
J1, J13, J16: 12V + GND (TP); ScrewTerminal_P3.5mm_2Pin_FP7x7
J3, J35, J36, J37, J38, J39: Conn_01x02_Pin; PinHeader_1x02_P2.54mm_Vertical
J4, J12, J19: 3V3 + GND (TP); ScrewTerminal_P3.5mm_2Pin_FP7x7
J5, J18: GND; ScrewTerminal_P5mm_2Pin_FP10x8
J8: RS485; ScrewTerminal_P5mm_3Pin_FP15x8
J10: SCL1 + GND (TP); ScrewTerminal_P3.5mm_2Pin_FP7x7
J11: SDA1 + GND (TP); ScrewTerminal_P3.5mm_2Pin_FP7x7
J14, J20: SCL6 + GND (TP); ScrewTerminal_P3.5mm_2Pin_FP7x7
J15, J21: SDA6 + GND (TP); ScrewTerminal_P3.5mm_2Pin_FP7x7
J17: 24V IN; ScrewTerminal_P5mm_2Pin_FP10x8
J22: SDA, SCL - ESP32; ScrewTerminal_P3.5mm_2Pin_FP7x7
J23: I2C7 Reserve SCL/GND; ScrewTerminal_P3.5mm_2Pin_FP7x7
J24: I2C6 Reserve SDA/GND; ScrewTerminal_P3.5mm_2Pin_FP7x7
J25: I2C7 Reserve SDA/GND; ScrewTerminal_P3.5mm_2Pin_FP7x7
J26: I2C6 Reserve SCL/GND; ScrewTerminal_P3.5mm_2Pin_FP7x7
J27, J28: CAT6-Shield; Shield_Landing_Pad_6mmCable_ZipTie
J29: Chassis; ScrewTerminal_P5mm_2Pin_FP10x8
J30: RX DIR; ScrewTerminal_P3.5mm_2Pin_FP7x7
J31: TX, GND; ScrewTerminal_P3.5mm_2Pin_FP7x7
J32: 12V out; ScrewTerminal_P5mm_3Pin_FP15x8
J33: 5V out; ScrewTerminal_P5mm_3Pin_FP15x8
J34: 3V3 out; ScrewTerminal_P5mm_3Pin_FP15x8
L1: 150u; L_Radial_D12.5mm_P7.00mm_Fastron_09HCP
L2: 330u; L_Radial_D10.5mm_P5.00mm_Abacron_AISR-01
L3: 470u; L_Toroid_Vertical_L21.6mm_W11.4mm_P7.62mm_Pulse_KM-3
R1, R2, R21, R22, R25, R26, R28, R29, R39, R40, R41, R42: 2k2; R_Axial_DIN0207_L6.3mm_D2.5mm_P10.16mm_Horizontal
R3, R4, R23, R24, R30, R31: 750; R_Axial_DIN0207_L6.3mm_D2.5mm_P10.16mm_Horizontal
R17, R18: 10k; R_Axial_DIN0207_L6.3mm_D2.5mm_P10.16mm_Horizontal
R27: 2.5; Cement-Power-R_L22_W10_P23_Horizontal
R32, R33: 10; R_Axial_DIN0207_L6.3mm_D2.5mm_P2.54mm_Vertical
R34, R38: 2k2; R_Axial_DIN0207_L6.3mm_D2.5mm_P2.54mm_Vertical
R35, R37: 470; R_Axial_DIN0207_L6.3mm_D2.5mm_P10.16mm_Horizontal
R36: 120; R_Axial_DIN0207_L6.3mm_D2.5mm_P10.16mm_Horizontal
R43: 1M; R_Axial_DIN0207_L6.3mm_D2.5mm_P10.16mm_Horizontal
R44, R45, R46, R47: 22; R_Axial_DIN0207_L6.3mm_D2.5mm_P10.16mm_Horizontal
R48, R49: 22; R_Axial_DIN0204_L3.6mm_D1.6mm_P7.62mm_Horizontal
TP1: 24V filtered; PinHeader_1x01_P1.00mm_Vertical
TP2: RX; PinHeader_1x01_P2.54mm_Vertical
TP3: TP A; PinHeader_1x01_P2.54mm_Vertical
TP4: DE; PinHeader_1x01_P2.54mm_Vertical
TP5: TP B; PinHeader_1x01_P2.54mm_Vertical
TP6: BATT; PinHeader_1x01_P1.00mm_Vertical
TP7: TX; PinHeader_1x01_P2.54mm_Vertical
TP8, TP12, TP13, TP26: GND; PinHeader_1x01_P2.54mm_Vertical
TP9: 5V; PinHeader_1x01_P2.54mm_Vertical
TP10: 12V; PinHeader_1x01_P2.54mm_Vertical
TP11: 3V3; PinHeader_1x01_P2.54mm_Vertical
TP14: SCL6; PinHeader_1x01_P2.54mm_Vertical
TP15: SDA6; PinHeader_1x01_P2.54mm_Vertical
TP16: SCL7; PinHeader_1x01_P2.54mm_Vertical
TP17: SDA7; PinHeader_1x01_P2.54mm_Vertical
TP18: Chassis; PinHeader_1x01_P2.54mm_Vertical
TP19: SCL; PinHeader_1x01_P2.54mm_Vertical
TP20: 12V-Filtered; PinHeader_1x01_P2.54mm_Vertical
TP21: 3V3-IN; PinHeader_1x01_P2.54mm_Vertical
TP22: 3V3-Filtered; PinHeader_1x01_P2.54mm_Vertical
TP23: SDA; PinHeader_1x01_P2.54mm_Vertical
TP24: SCL-in; PinHeader_1x01_P2.54mm_Vertical
TP25: SDA-in; PinHeader_1x01_P2.54mm_Vertical
U1: MAX3485; DIP-8_W7.62mm_LongPads
U2, U8, U14: PCA9600D; Adapter-Board_SOP8_to_DIP8
U3: TCA9548A_1-to-8_I2C_Multiplexer_Breakout-Board; TCA9548A_1-to-8_I2C_Multiplexer_Breakout_Board
U4: LM2576T-3.3; TO-220-5_P3.4x3.7mm_StaggerOdd_Lead3.8mm_Vertical
U9: LM2576T-5; TO-220-5_P3.4x3.7mm_StaggerOdd_Lead3.8mm_Vertical
U10: LM2576T-12; TO-220-5_P3.4x3.7mm_StaggerOdd_Lead3.8mm_Vertical
U13: AS5600_Breakout; AS5600_Magnetic-Encoder_Breakout_Board
a1: ICM-426XX_Breakout; ICM-426XX_6-Axis-Gyro_Breakout_Board

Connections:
+3V3: C1.1, C3.1, C10.1, D19.2 (K), D23.2 (K), D24.2 (K), D25.2 (K), J4.1, J12.1, J34.1, J34.2, J34.3, L1.2, R1.1, R2.1, R17.1, R18.1, R21.1, R22.1, R25.1, R26.1, R34.1, R35.1, R38.1, R39.1, R40.1, R41.1, R42.1, TP11.1, U1.8 (VCC), U3.1 (VIN), U4.4 (FB), a1.1 (VCC)
+3V3_REMOTE: C12.1, C13.1, R28.1, R29.1, R33.1, TP22.1, U13.1 (VCC)
+5V: C6.1, J33.1, J33.2, J33.3, L2.2, TP9.1, U9.4 (FB)
+12V: C8.1, C14.1, C15.1, C16.1, C17.1, D7.2 (K), D10.2 (K), D21.2 (K), D22.2 (K), J1.1, J13.1, J32.1, J32.2, J32.3, L3.2, R3.1, R4.1, R23.1, R24.1, TP10.1, U2.8 (VCC), U8.8 (VCC), U10.4 (FB)
+12V_REMOTE: C9.1, C11.1, C18.1, C19.1, D14.2 (K), D26.2 (K), R30.1, R31.1, R32.1, TP20.1, U14.8 (VCC)
+24V filtered: C2.1, C4.1, C5.1, C7.1, D3.2 (A2), R27.2, TP1.1, U4.1 (VIN), U9.1 (VIN), U10.1 (VIN)
+BATT: F2.2, J17.1, J17.2
/ESP32_SCL: J22.2, R38.2, R48.2
/ESP32_SDA: J22.1, R34.2, R49.2
/I2C0_SCL: J39.1, R2.2, U2.1 (SX), U3.10 (SCL0)
/I2C0_SDA: J39.2, R1.2, U2.7 (SY), U3.9 (SDA0)
/I2C1_SCL: J38.1, R22.2, U3.12 (SCL1), U8.1 (SX)
/I2C1_SDA: J38.2, R21.2, U3.11 (SDA1), U8.7 (SY)
/I2C2_SCL: J3.1, U3.14 (SCL2)
/I2C2_SDA: J3.2, U3.13 (SDA2)
/I2C3_SCL: J35.1, U3.16 (SCL3)
/I2C3_SDA: J35.2, U3.15 (SDA3)
/I2C4_SCL: J36.1, U3.18 (SCL4)
/I2C4_SDA: J36.2, U3.17 (SDA4)
/I2C5_SCL: J37.1, R25.2, U3.20 (SCL5), a1.3 (SCL)
/I2C5_SDA: J37.2, R26.2, U3.19 (SDA5), a1.4 (SDA)
/I2C6_SCL: D25.3 (COM), R46.2, U3.22 (SCL6)
/I2C6_SDA: D24.3 (COM), R47.2, U3.21 (SDA6)
/I2C7_SCL: D23.3 (COM), R44.2, U3.24 (SCL7)
/I2C7_SDA: D19.3 (COM), R45.2, U3.23 (SDA7)
/MASTER_SCL: R48.1, U3.4 (SCL)
/MASTER_SDA: R49.1, U3.3 (SDA)
/RS485-A: D13.2 (A2), J8.2, R35.2, R36.2, TP3.1, U1.6 (A)
/RS485-B: D13.1 (A1), J8.3, R36.1, R37.1, TP5.1, U1.7 (B)
/RS485_DIR: J30.1, R17.2, TP4.1, U1.2 (~RE), U1.3 (DE)
/RS485_RX: J30.2, TP2.1, U1.1 (RO)
/RS485_TX: J31.2, TP7.1, U1.4 (DI)
/Remote-I2C-Sensor-Board/3V3_REMOTE-IN: FB1.1, J19.1, TP21.1
/Remote-I2C-Sensor-Board/12V_REMOTE-IN: FB3.1, J16.1
/Remote-I2C-Sensor-Board/SCL_AS5600: R29.2, TP19.1, U13.6 (SCL), U14.1 (SX)
/Remote-I2C-Sensor-Board/SCL_REMOTE-IN: D16.2 (A2), D26.3 (COM), J20.1, R30.2, TP24.1, U14.2 (RX), U14.3 (TX)
/Remote-I2C-Sensor-Board/SDA_AS5600: R28.2, TP23.1, U13.5 (SDA), U14.7 (SY)
/Remote-I2C-Sensor-Board/SDA_REMOTE-IN: D12.2 (A2), D14.3 (COM), J21.1, R31.2, TP25.1, U14.5 (TY), U14.6 (RY)
/SCL_Boost1: D9.2 (A2), D22.3 (COM), J14.2, R3.2, U2.2 (RX), U2.3 (TX)
/SCL_Boost2: D10.3 (COM), D31.2 (A2), J10.2, R23.2, U8.2 (RX), U8.3 (TX)
/SDA_Boost1: D11.2 (A2), D21.3 (COM), J15.2, R4.2, U2.5 (TY), U2.6 (RY)
/SDA_Boost2: D7.3 (COM), D8.2 (A2), J11.2, R24.2, U8.5 (TY), U8.6 (RY)
Chassis: C20.2, H2.1, J27.1, J28.1, J29.1, J29.2, R43.1, TP18.1
GND: C1.2, C2.2, C3.2, C4.2, C5.2, C6.2, C7.2, C8.2, C10.2, C14.2, C15.2, C16.2, C17.2, C20.1, D1.2 (A), D2.2 (A), D3.1 (A1), D4.2 (A), D5.2 (A), D6.2 (A2), D7.1 (A), D8.1 (A1), D9.1 (A1), D10.1 (A), D11.1 (A1), D13.3 (common), D17.2 (A2), D18.2 (A2), D19.1 (A), D20.2 (A2), D21.1 (A), D22.1 (A), D23.1 (A), D24.1 (A), D25.1 (A), D31.1 (A1), H1.1, H3.1, H4.1, J1.2, J4.2, J5.1, J5.2, J8.1, J10.1, J11.1, J12.2, J13.2, J14.1, J15.1, J18.1, J18.2, J23.2, J24.2, J25.2, J26.2, J31.1, R37.2, R43.2, TP8.1, TP13.1, U1.5 (GND), U2.4 (GND), U3.2 (GND), U3.6 (A0), U3.7 (A1), U3.8 (A2), U4.3 (GND), U4.5 (~ON/OFF), U8.4 (GND), U9.3 (GND), U9.5 (~ON/OFF), U10.3 (GND), U10.5 (~ON/OFF), a1.2 (GND)
GND_REMOTE: C9.2, C11.2, C12.2, C13.2, C18.2, C19.2, D12.1 (A1), D14.1 (A), D16.1 (A1), D26.1 (A), H5.1, H6.1, H7.1, H8.1, J16.2, J19.2, J20.2, J21.2, TP12.1, TP26.1, U13.3 (GND), U14.4 (GND)
unnamed: D1.1 (K), F2.1, R27.1, TP6.1
unnamed: D2.1 (K), L1.1, U4.2 (OUT)
unnamed: D4.1 (K), L2.1, U9.2 (OUT)
unnamed: D5.1 (K), L3.1, U10.2 (OUT)
unnamed: D6.1 (A1), J25.1, R40.2, R45.1, TP17.1
unnamed: D17.1 (A1), J24.1, R42.2, R47.1, TP15.1
unnamed: D18.1 (A1), J23.1, R39.2, R44.1, TP16.1
unnamed: D20.1 (A1), J26.1, R41.2, R46.1, TP14.1
unnamed: FB1.2, R33.2
unnamed: FB3.2, R32.2
unnamed: R18.2, U3.5 (RST)

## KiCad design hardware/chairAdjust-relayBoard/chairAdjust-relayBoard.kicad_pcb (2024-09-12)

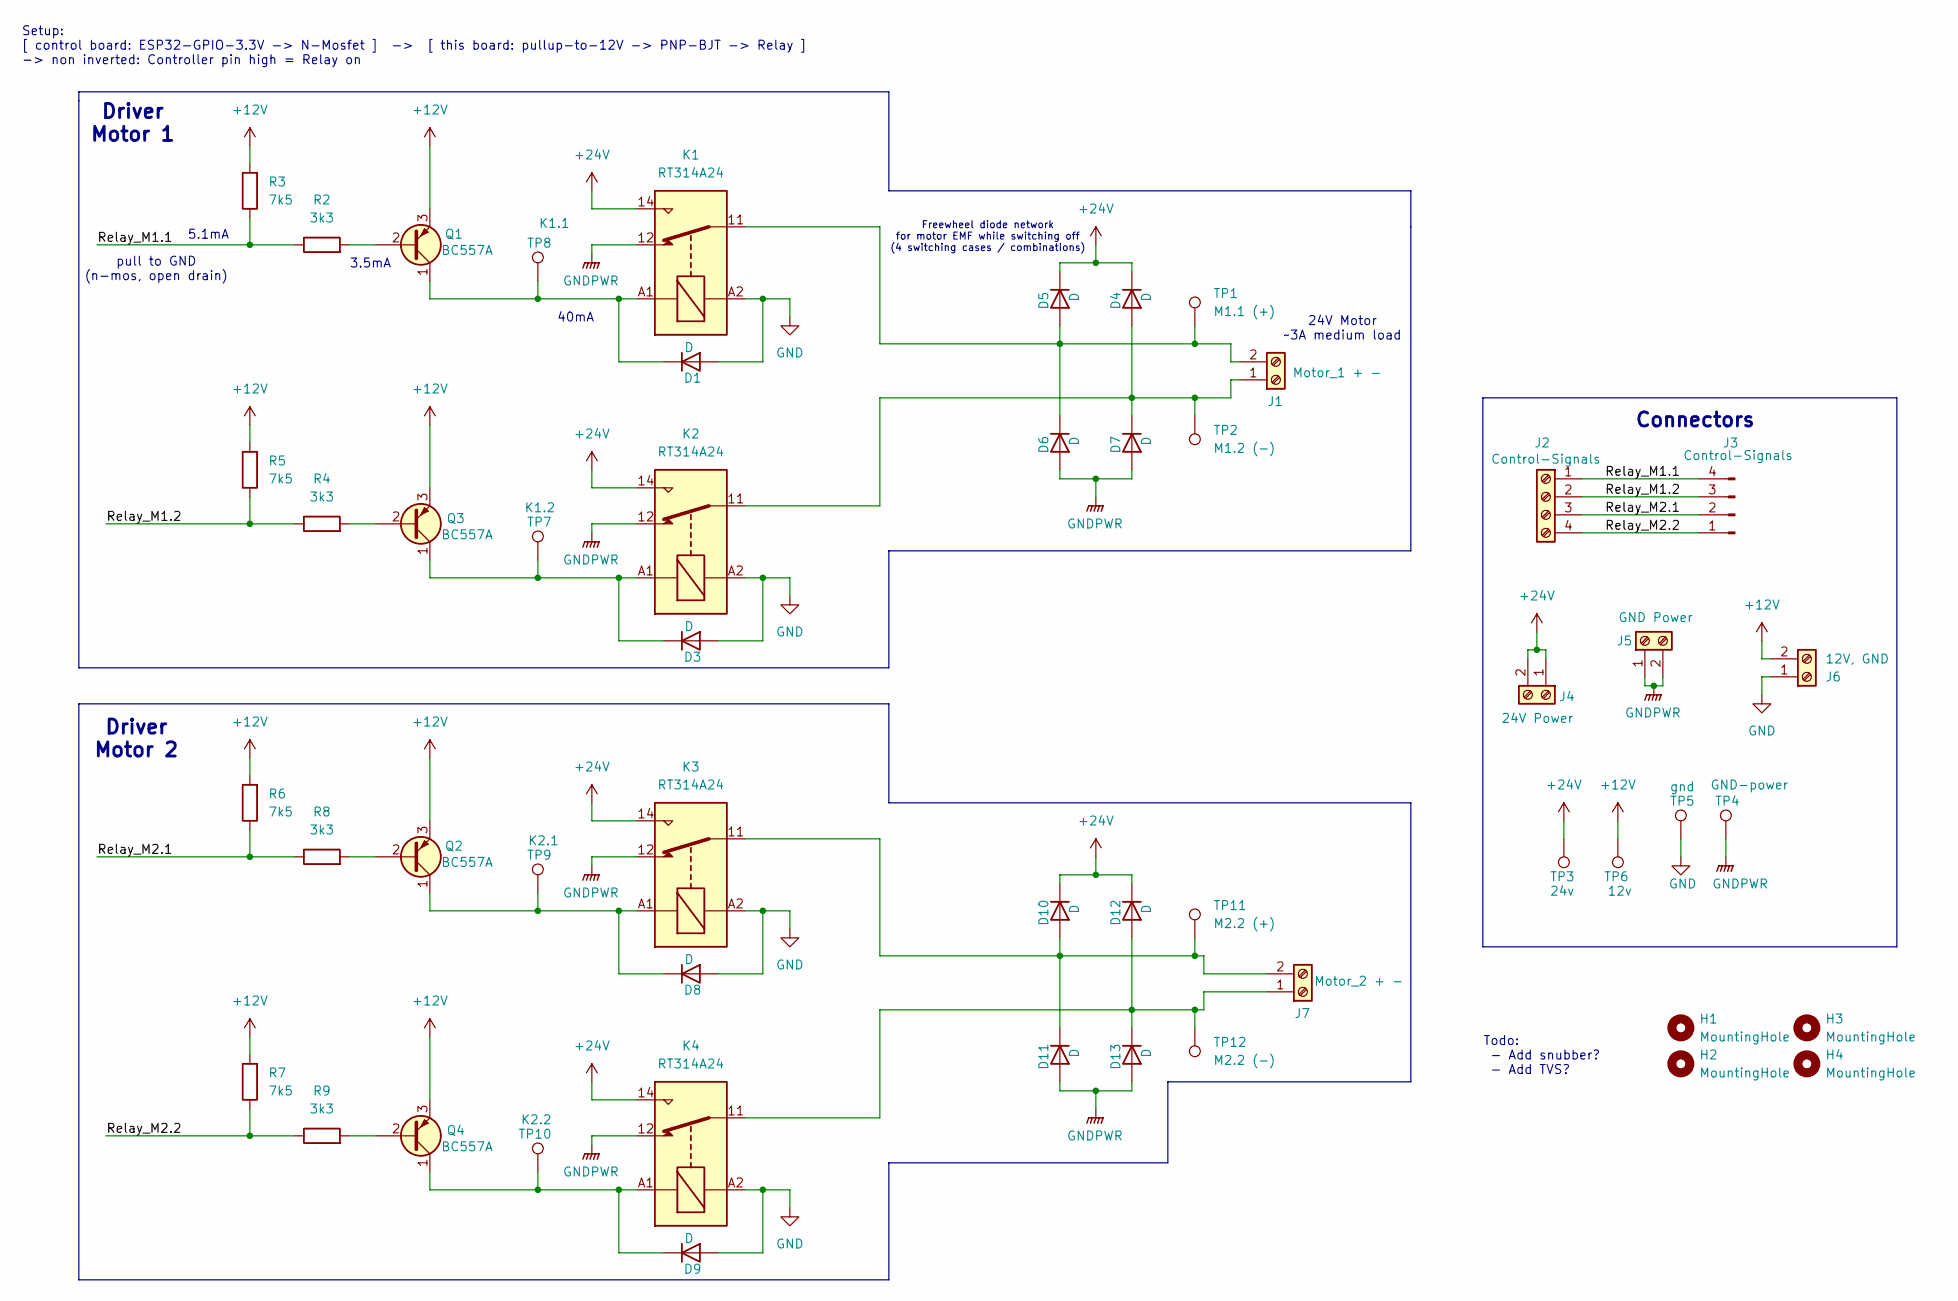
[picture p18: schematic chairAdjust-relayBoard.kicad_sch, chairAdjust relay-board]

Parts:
D1, D3, D8, D9: D; D_5W_P12.70mm_Horizontal
D4, D5, D6, D7, D10, D11, D12, D13: D; D_DO-27_P20.32mm_Horizontal
H1, H2, H3, H4: MountingHole; MountingHole_5.3mm_M5
J1: Motor_1 + -; TerminalBlock_bornier-2_P5.08mm
J2: Control-Signals; TerminalBlock_4Ucon_1x04_P3.50mm_Horizontal
J3: Control-Signals; PinHeader_1x04_P2.54mm_Vertical
J4: 24V Power; TerminalBlock_bornier-2_P5.08mm
J5: GND Power; TerminalBlock_bornier-2_P5.08mm
J6: 12V, GND; TerminalBlock_bornier-2_P5.08mm
J7: Motor_2 + -; TerminalBlock_bornier-2_P5.08mm
K1, K2, K3, K4: RT314A24; Relay_SPDT_Schrack-RT1-16A-FormC_RM5mm
Q1, Q2, Q3, Q4: BC557A; TO-92_Inline_Wide_CBE
R2, R4, R8, R9: 3k3; R_Axial_DIN0207_L6.3mm_D2.5mm_P10.16mm_Horizontal
R3, R5, R6, R7: 7k5; R_Axial_DIN0207_L6.3mm_D2.5mm_P10.16mm_Horizontal
TP1: M1.1 (+); PinHeader_1x01_P1.00mm_Vertical
TP2: M1.2 (-); PinHeader_1x01_P1.00mm_Vertical
TP3: 24v; PinHeader_1x01_P1.00mm_Vertical
TP4: GND-power; PinHeader_1x01_P1.00mm_Vertical
TP5: gnd; PinHeader_1x01_P1.00mm_Vertical
TP6: 12v; PinHeader_1x01_P1.00mm_Vertical
TP7: K1.2; PinHeader_1x01_P1.00mm_Vertical
TP8: K1.1; PinHeader_1x01_P1.00mm_Vertical
TP9: K2.1; PinHeader_1x01_P1.00mm_Vertical
TP10: K2.2; PinHeader_1x01_P1.00mm_Vertical
TP11: M2.2 (+); PinHeader_1x01_P1.00mm_Vertical
TP12: M2.2 (-); PinHeader_1x01_P1.00mm_Vertical

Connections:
+12V: J6.2, Q1.3 (E), Q2.3 (E), Q3.3 (E), Q4.3 (E), R3.2, R5.2, R6.2, R7.2, TP6.1
+24V: D4.1 (K), D5.1 (K), D10.1 (K), D12.1 (K), J4.1, J4.2, K1.14, K2.14, K3.14, K4.14, TP3.1
/Relay_M1.1: J2.1, J3.4, R2.1, R3.1
/Relay_M1.2: J2.2, J3.3, R4.1, R5.1
/Relay_M2.1: J2.3, J3.2, R6.1, R8.1
/Relay_M2.2: J2.4, J3.1, R7.1, R9.1
GND: D1.2 (A), D3.2 (A), D8.2 (A), D9.2 (A), J6.1, K1.A2, K2.A2, K3.A2, K4.A2, TP5.1
GNDPWR: D6.2 (A), D7.2 (A), D11.2 (A), D13.2 (A), J5.1, J5.2, K1.12, K2.12, K3.12, K4.12, TP4.1
unnamed: D1.1 (K), K1.A1, Q1.1 (C), TP8.1
unnamed: D3.1 (K), K2.A1, Q3.1 (C), TP7.1
unnamed: D4.2 (A), D7.1 (K), J1.1, K2.11, TP2.1
unnamed: D5.2 (A), D6.1 (K), J1.2, K1.11, TP1.1
unnamed: D8.1 (K), K3.A1, Q2.1 (C), TP9.1
unnamed: D9.1 (K), K4.A1, Q4.1 (C), TP10.1
unnamed: D10.2 (A), D11.1 (K), J7.2, K3.11, TP11.1
unnamed: D12.2 (A), D13.1 (K), J7.1, K4.11, TP12.1
unnamed: Q1.2 (B), R2.2
unnamed: Q2.2 (B), R8.2
unnamed: Q3.2 (B), R4.2
unnamed: Q4.2 (B), R9.2

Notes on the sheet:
Driver Motor 2
Connectors
Setup: [ control board: ESP32-GPIO-3.3V -> N-Mosfet ] -> [ this board: pullup-to-12V -> PNP-BJT -> Relay ] -> non inverted: Controller pin high = Relay on
24V Motor ~3A medium load
pull to GND (n-mos, open drain)
40mA
Driver Motor 1
Todo: - Add snubber? - Add TVS?
Freewheel diode network for motor EMF while switching off (4 switching cases / combinations)
5.1mA
3.5mA

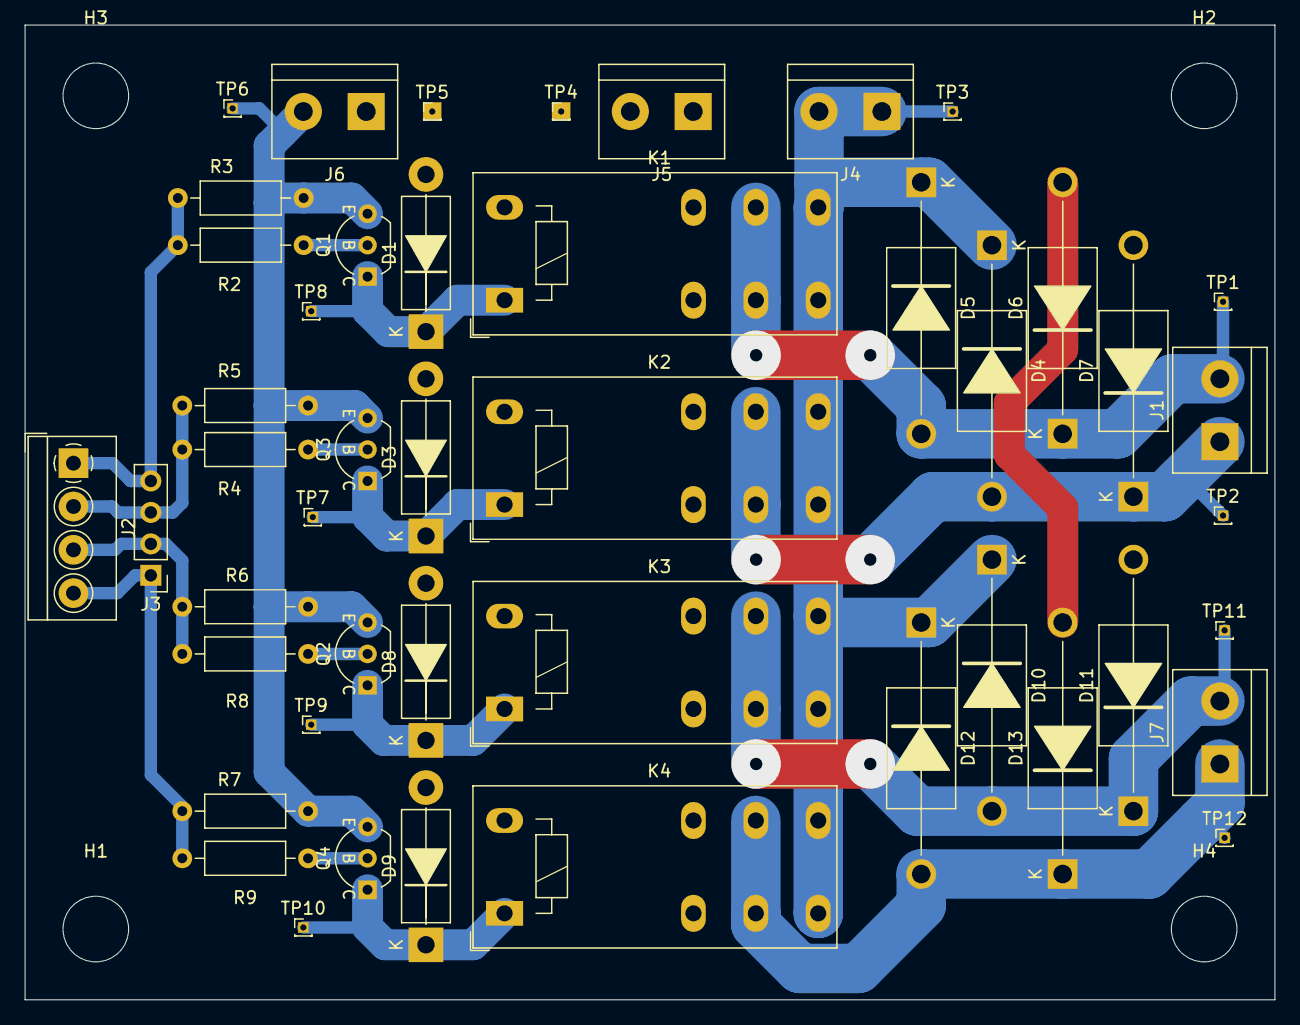
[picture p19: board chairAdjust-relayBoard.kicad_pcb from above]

Board: 2 copper layers, 101.0 x 78.7 mm, 51 parts (0 on the bottom side), 20 nets.

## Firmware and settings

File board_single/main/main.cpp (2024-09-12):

extern "C"
{
#include <stdio.h>
#include <esp_system.h>
#include <esp_event.h>
#include <nvs_flash.h>
#include "nvs.h"
#include "freertos/FreeRTOS.h"
#include "freertos/task.h"
#include "driver/gpio.h"
#include "esp_log.h"
#include "sdkconfig.h"
#include "esp_spiffs.h"    

//custom C files
#include "wifi.h"
}

#include <new>

//custom C++ files
//folder common
#include "uart_common.hpp"
#include "motordrivers.hpp"
#include "http.hpp"
#include "speedsensor.hpp"
#include "motorctl.hpp"

//folder single_board
#include "control.hpp" 
#include "button.hpp"
#include "display.hpp"
#include "encoder.hpp"

//only extends this file (no library):
//outsourced all configuration related structures
#include "config.cpp"



//================================
//======== declarations ==========
//================================
//--- declare all pointers to shared objects ---
controlledMotor *motorLeft;
controlledMotor *motorRight;

// TODO initialize driver in createOjects like everything else
// (as in 6e9b3d96d96947c53188be1dec421bd7ff87478e) 
// issue with laggy encoder wenn calling methods via pointer though
//sabertooth2x60a *sabertoothDriver;
sabertooth2x60a sabertoothDriver(sabertoothConfig);

evaluatedJoystick *joystick;

buzzer_t *buzzer;

controlledArmchair *control;

automatedArmchair_c *automatedArmchair;

httpJoystick *httpJoystickMain;

speedSensor *speedLeft;
speedSensor *speedRight;

cControlledRest *legRest;
cControlledRest *backRest;


//--- lambda functions motor-driver ---
// functions for updating the duty via currently used motor driver (hardware) that can then be passed to controlledMotor
//-> makes it possible to easily use different motor drivers
motorSetCommandFunc_t setLeftFunc = [&sabertoothDriver](motorCommand_t cmd)
{
	//TODO why encoder lag when call via pointer?
    sabertoothDriver.setLeft(cmd);
};
motorSetCommandFunc_t setRightFunc = [&sabertoothDriver](motorCommand_t cmd)
{
    sabertoothDriver.setRight(cmd);
};

//--- lambda function http-joystick ---
// function that initializes the http server requires a function pointer to function that handels each url
// the httpd_uri config struct does not accept a pointer to a method of a class instance, directly
// thus this lambda function is necessary:
// declare pointer to receiveHttpData method of httpJoystick class
esp_err_t (httpJoystick::*pointerToReceiveFunc)(httpd_req_t *req) = &httpJoystick::receiveHttpData;
esp_err_t on_joystick_url(httpd_req_t *req)
{
    // run pointer to receiveHttpData function of httpJoystickMain instance
    return (httpJoystickMain->*pointerToReceiveFunc)(req);
}

//--- tag for logging ---
static const char * TAG = "main";

//-- handle passed to tasks for accessing nvs --
nvs_handle_t nvsHandle;




//=================================
//========== init spiffs ==========
//=================================
//initialize spi flash filesystem (used for webserver)
void init_spiffs(){
    esp_vfs_spiffs_conf_t esp_vfs_spiffs_conf = {
        .base_path = "/spiffs",
        .partition_label = NULL,
        .max_files = 5,
        .format_if_mount_failed = true};
    esp_vfs_spiffs_register(&esp_vfs_spiffs_conf);

    size_t total = 0;
    size_t used = 0;
    esp_spiffs_info(NULL, &total, &used);

    ESP_LOGI(TAG, "SPIFFS: total %d, used %d", total, used);
    esp_vfs_spiffs_unregister(NULL);
}




//=================================
//========= createObjects =========
//=================================
//create all shared objects
//their references can be passed to the tasks that need access in main

//Note: the configuration structures (e.g. configMotorControlLeft) are outsourced to file 'config.cpp'

void createObjects()
{
    // create sabertooth motor driver instance
    // sabertooth2x60a sabertoothDriver(sabertoothConfig);
    // with configuration above
	//sabertoothDriver = new sabertooth2x60a(sabertoothConfig);

    // create speedsensor instances
    // with configurations from config.cpp
    speedLeft = new speedSensor(speedLeft_config);
    speedRight = new speedSensor(speedRight_config);

	// create controlled motor instances (motorctl.hpp)
    // with configurations from config.cpp
    motorLeft = new controlledMotor(setLeftFunc, configMotorControlLeft, &nvsHandle, speedLeft, &motorRight); //note: ptr to ptr of controlledMotor since it isnt defined yet
    motorRight = new controlledMotor(setRightFunc, configMotorControlRight, &nvsHandle, speedRight, &motorLeft);

    // create joystick instance (joystick.hpp)
    joystick = new evaluatedJoystick(configJoystick, &nvsHandle);

    // create httpJoystick object (http.hpp)
    httpJoystickMain = new httpJoystick(configHttpJoystickMain);
    http_init_server(on_joystick_url);

    // create buzzer object on pin 12 with gap between queued events of 1ms
    buzzer = new buzzer_t(GPIO_NUM_12, 1);

    // create objects for controlling the chair position
    //                       gpio_up, gpio_down, travelDuration, name, defaultPosition
    legRest = new cControlledRest(GPIO_NUM_2, GPIO_NUM_15, 11000, "legRest");
    backRest = new cControlledRest(GPIO_NUM_16, GPIO_NUM_4, 12000, "backRest", 5); //default position "100% up"

    // create control object (control.hpp)
    // with configuration from config.cpp
    control = new controlledArmchair(configControl, buzzer, motorLeft, motorRight, joystick, &joystickGenerateCommands_config, httpJoystickMain, automatedArmchair, legRest, backRest, &nvsHandle);

    // create automatedArmchair_c object (for auto-mode) (auto.hpp)
    automatedArmchair = new automatedArmchair_c(motorLeft, motorRight);

}




//=================================
//=========== app_main ============
//=================================
extern "C" void app_main(void) {
	ESP_LOGW(TAG, "===== BOOT (pre main) Completed =====\n");

	ESP_LOGW(TAG, "===== INITIALIZING COMPONENTS =====");
	//--- define log levels ---
	setLoglevels();

	//--- enable 5V volate regulator ---
	ESP_LOGW(TAG, "enabling 5V regulator...");
	gpio_pad_select_gpio(GPIO_NUM_17);                                                  
	gpio_set_direction(GPIO_NUM_17, GPIO_MODE_OUTPUT);
	gpio_set_level(GPIO_NUM_17, 1);                                                      

	//--- initialize nvs-flash and netif ---
	ESP_LOGW(TAG,"initializing NVS...");
	wifi_initNvs(); //needed for wifi and persistent config variables
	ESP_LOGW(TAG,"initializing NETIF...");
	wifi_initNetif(); // needed for wifi

	//--- initialize spiffs ---
    ESP_LOGW(TAG, "initializing SPIFFS...");
	init_spiffs(); // used by httpd server

	//--- initialize and start wifi ---
	// Note: now started only when switching to HTTP mode in control.cpp
	// ESP_LOGW(TAG,"starting wifi...");
	// wifi_start_client(); //connect to existing wifi (dropped)
	// wifi_start_ap(); //start access point

	//--- initialize encoder ---
	const QueueHandle_t encoderQueue = encoder_init(&encoder_config);

	//--- open nvs-flash ---
	// note: nvs already initialized in wifi_initNvs()
    ESP_LOGW(TAG, "opening NVS-handle...");
	esp_err_t err = nvs_open("storage", NVS_READWRITE, &nvsHandle); // this handle is passed to all tasks for accessing nvs
	if (err != ESP_OK)
		ESP_LOGE(TAG, "Error (%s) opening NVS handle!\n", esp_err_to_name(err));

	printf("\n");



	//--- create all objects ---
	ESP_LOGW(TAG, "===== CREATING SHARED OBJECTS =====");

	//initialize sabertooth object in STACK (due to performance issues in heap)
	///sabertoothDriver = static_cast<sabertooth2x60a*>(alloca(sizeof(sabertooth2x60a)));
	///new (sabertoothDriver) sabertooth2x60a(sabertoothConfig);

	//create all class instances used below in HEAP
	createObjects();

	printf("\n");



	//--- create tasks ---
	ESP_LOGW(TAG, "===== CREATING TASKS =====");

	//----------------------------------------------
	//--- create task for controlling the motors ---
	//----------------------------------------------
	//task for each motor that handles to following:
	//receives commands from control via queue, handle ramp and current, apply new duty by passing it to method of motordriver (ptr)
	xTaskCreate(&task_motorctl, "task_ctl-left-motor", 2*4096, motorLeft, 6, NULL);
	xTaskCreate(&task_motorctl, "task_ctl-right-motor", 2*4096, motorRight, 6, NULL);

	//------------------------------
	//--- create task for buzzer ---
	//------------------------------
	//task that processes queued beeps
	//note: pointer to shard object 'buzzer' is passed as task parameter:
	xTaskCreate(&task_buzzer, "task_buzzer", 2048, buzzer, 2, NULL);

	//-------------------------------
	//--- create task for control ---
	//-------------------------------
	//task that generates motor commands depending on the current mode and sends those to motorctl task
	//note: pointer to shared object 'control' is passed as task parameter:
	xTaskCreate(&task_control, "task_control", 4096, control, 5, NULL);

	//------------------------------
	//--- create task for button ---
	//------------------------------
	//task that handles button/encoder events in any mode except 'MENU_SETTINGS' and 'MENU_MODE_SELECT' (e.g. switch modes by pressing certain count)
	task_button_parameters_t button_param = {control, joystick, encoderQueue, motorLeft, motorRight, legRest, backRest, buzzer};
	xTaskCreate(&task_button, "task_button", 4096, &button_param, 3, NULL);

	//-----------------------------------
	//--- create task for fan control ---
	//-----------------------------------
	//task that controls cooling fans of the motor driver
	task_fans_parameters_t fans_param = {configFans, motorLeft, motorRight};
	xTaskCreate(&task_fans, "task_fans", 2048, &fans_param, 1, NULL);

	//-----------------------------------
	//----- create task for display -----
	//-----------------------------------
	//task that handles the display (show stats, handle menu in 'MENU_SETTINGS' and 'MENU_MODE_SELECT' mode)
	display_task_parameters_t display_param = {display_config, control, joystick, encoderQueue, motorLeft, motorRight, speedLeft, speedRight, buzzer, &nvsHandle};
	xTaskCreate(&display_task, "display_task", 3*2048, &display_param, 3, NULL);
	
	//-------------------------------------
	//-- create task for chairAdjustment --
	//-------------------------------------
	//tasks that stop chair-rest motors when they reach target (note: they sleep when motors not running)
	xTaskCreate(&chairAdjust_task, "chairAdjustLeg_task", 2048, legRest, 1, NULL);
	xTaskCreate(&chairAdjust_task, "chairAdjustBack_task", 2048, backRest, 1, NULL);

	vTaskDelay(200 / portTICK_PERIOD_MS); //wait for all tasks to finish initializing
	printf("\n");



	//--- startup finished ---
	ESP_LOGW(TAG, "===== STARTUP FINISHED =====\n");
	buzzer->beep(3, 70, 50);

	//--- testing encoder ---
	//xTaskCreate(&task_encoderExample, "task_buzzer", 2048, encoderQueue, 2, NULL);

	//--- testing http server ---
	//    wifi_init_client(); //connect to existing wifi
	//    vTaskDelay(2000 / portTICK_PERIOD_MS);
	//    ESP_LOGI(TAG, "initializing http server");
	//    http_init_server();


	//--- testing force specific mode after startup ---
	//control->changeMode(controlMode_t::MENU_SETTINGS);



	//--- main loop ---
	//does nothing except for testing things
	while(1){
		vTaskDelay(portMAX_DELAY);
		//vTaskDelay(5000 / portTICK_PERIOD_MS);

		//---------------------------------
		//-------- TESTING section --------
		//---------------------------------
		//test sabertooth driver
		//		motors.setLeft({motorstate_t::FWD, 70});
		//		vTaskDelay(1000 / portTICK_PERIOD_MS);
		//		motors.setLeft({motorstate_t::IDLE, 0});
		//		vTaskDelay(1000 / portTICK_PERIOD_MS);
		//		motors.setLeft({motorstate_t::REV, 50});
		//		vTaskDelay(1000 / portTICK_PERIOD_MS);
		//		motors.setLeft(-90);
		//		vTaskDelay(1000 / portTICK_PERIOD_MS);
		//		motors.setLeft(90);
		//		vTaskDelay(1000 / portTICK_PERIOD_MS);
		//		motors.setLeft(0);
		//		vTaskDelay(1000 / portTICK_PERIOD_MS);


		//--- test controlledMotor --- (ramp)
		// //brake for 1 s
		//motorLeft.setTarget(motorstate_t::BRAKE);
		//vTaskDelay(1000 / portTICK_PERIOD_MS);
		//command 90% - reverse
		//motorLeft.setTarget(motorstate_t::REV, 90);
		//vTaskDelay(5000 / portTICK_PERIOD_MS);
		//motorLeft.setTarget(motorstate_t::FWD, 80);
		//vTaskDelay(1000 / portTICK_PERIOD_MS);
		//motorLeft.setTarget(motorstate_t::IDLE, 90);
		//vTaskDelay(1000 / portTICK_PERIOD_MS);


		// //--- test functions at mode change HTTP ---
		// control.changeMode(controlMode_t::HTTP);
		// vTaskDelay(10000 / portTICK_PERIOD_MS);
		// control.changeMode(controlMode_t::IDLE);
		// vTaskDelay(10000 / portTICK_PERIOD_MS);


		//--- test wifi functions ---
		// ESP_LOGI(TAG, "creating AP");
		// wifi_init_ap(); //start accesspoint
		// vTaskDelay(15000 / portTICK_PERIOD_MS);
		// ESP_LOGI(TAG, "stopping wifi");
		// wifi_deinit_ap();  //stop wifi access point
		// vTaskDelay(5000 / portTICK_PERIOD_MS);
		// ESP_LOGI(TAG, "connecting to wifi");
		// wifi_init_client(); //connect to existing wifi
		// vTaskDelay(10000 / portTICK_PERIOD_MS);
		// ESP_LOGI(TAG, "stopping wifi");
		// wifi_deinit_client(); //stop wifi client
		// vTaskDelay(5000 / portTICK_PERIOD_MS);


		//--- test button ---
		//buttonJoystick.handle();
		// if (buttonJoystick.risingEdge){
		//     ESP_LOGI(TAG, "button pressed, was released for %d ms", buttonJoystick.msReleased);
		//     buzzer.beep(2, 100, 50);

		// }else if (buttonJoystick.fallingEdge){
		//     ESP_LOGI(TAG, "button released, was pressed for %d ms", buttonJoystick.msPressed);
		//     buzzer.beep(1, 200, 0);
		// }


		//--- test joystick commands ---
		// motorCommands_t commands = joystick_generateCommandsDriving(joystick);
		// motorRight.setTarget(commands.right.state, commands.right.duty); //TODO make motorctl.setTarget also accept motorcommand struct directly
		// motorLeft.setTarget(commands.left.state, commands.left.duty); //TODO make motorctl.setTarget also accept motorcommand struct directly
		// //motorRight.setTarget(commands.right.state, commands.right.duty);


		//--- test joystick class ---
		//joystickData_t data = joystick.getData();
		//ESP_LOGI(TAG, "position=%s, x=%.1f%%, y=%.1f%%, radius=%.1f%%, angle=%.2f",
		//        joystickPosStr[(int)data.position], data.x*100, data.y*100, data.radius*100, data.angle);

		//--- test the motor driver ---
		//fade up duty - forward
		//   for (int duty=0; duty<=100; duty+=5) {
		//       motorLeft.setTarget(motorstate_t::FWD, duty);
		//       vTaskDelay(100 / portTICK_PERIOD_MS); 
		//   }


	}

}

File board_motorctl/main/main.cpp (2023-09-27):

extern "C"
{
#include <stdio.h>
#include <esp_system.h>
#include <esp_event.h>
#include <nvs_flash.h>
#include "freertos/FreeRTOS.h"
#include "freertos/task.h"
#include "driver/gpio.h"
#include "esp_log.h"
#include "sdkconfig.h"
#include "esp_spiffs.h"    
#include <string.h>

#include "driver/ledc.h"

	//custom C files
#include "wifi.h"
}
//custom C++ files
#include "config.hpp"
#include "uart.hpp"
#include "speedsensor.hpp"


//============================
//======= TESTING MODE =======
//============================
//do not start the actual tasks for controlling the armchair
#define TESTING_MODE

//=========================
//======= UART TEST =======
//=========================
//only run uart test code at the end
//disables other functionality
//#define UART_TEST_ONLY

//==========================
//======= BRAKE TEST =======
//==========================
//only run brake-test (ignore uart input)
//#define BRAKE_TEST_ONLY

//====================-======
//==== SPEED SENSOR TEST ====
//======================-====
//only run speed-sensor test
#define SPEED_SENSOR_TEST

//tag for logging
static const char * TAG = "main";


//====================================
//========== motorctl task ===========
//====================================
//task for handling the motors (ramp, current limit, driver)
void task_motorctl( void * pvParameters ){
	ESP_LOGI(TAG, "starting handle loop...");
	while(1){
		motorRight.handle();
		motorLeft.handle();
		//10khz -> T=100us
		vTaskDelay(10 / portTICK_PERIOD_MS);
	}
}



//======================================
//============ buzzer task =============
//======================================
//TODO: move the task creation to buzzer class (buzzer.cpp)
//e.g. only have function buzzer.createTask() in app_main
void task_buzzer( void * pvParameters ){
	ESP_LOGI("task_buzzer", "Start of buzzer task...");
	//run function that waits for a beep events to arrive in the queue
	//and processes them
	buzzer.processQueue();
}



//=======================================
//============== fan task ===============
//=======================================
//task that controlls fans for cooling the drivers
void task_fans( void * pvParameters ){
	ESP_LOGI(TAG, "Initializing fans and starting fan handle loop");
	//create fan instances with config defined in config.cpp
	controlledFan fan(configCooling, &motorLeft, &motorRight);
	//repeatedly run fan handle function in a slow loop
	while(1){
		fan.handle();
		vTaskDelay(500 / portTICK_PERIOD_MS);
	}
}



//==================================
//======== define loglevels ========
//==================================
void setLoglevels(void){
	//set loglevel for all tags:
	esp_log_level_set("*", ESP_LOG_WARN);

	//--- set loglevel for individual tags ---
	esp_log_level_set("main", ESP_LOG_INFO);
	esp_log_level_set("buzzer", ESP_LOG_ERROR);
	esp_log_level_set("motordriver", ESP_LOG_VERBOSE);
	esp_log_level_set("motor-control", ESP_LOG_INFO);
	//esp_log_level_set("evaluatedJoystick", ESP_LOG_DEBUG);
	//esp_log_level_set("joystickCommands", ESP_LOG_DEBUG);
	esp_log_level_set("button", ESP_LOG_INFO);
	esp_log_level_set("control", ESP_LOG_INFO);
	esp_log_level_set("fan-control", ESP_LOG_INFO);
	esp_log_level_set("wifi", ESP_LOG_INFO);
	esp_log_level_set("http", ESP_LOG_INFO);
	esp_log_level_set("automatedArmchair", ESP_LOG_DEBUG);
	esp_log_level_set("uart_common", ESP_LOG_INFO);
	esp_log_level_set("uart", ESP_LOG_INFO);
	//esp_log_level_set("current-sensors", ESP_LOG_INFO);
	esp_log_level_set("speedSensor", ESP_LOG_WARN);
}



//=================================
//=========== app_main ============
//=================================
extern "C" void app_main(void) {

	//---- define log levels ----
	setLoglevels();

#ifndef TESTING_MODE
	//enable 5V volate regulator
	gpio_pad_select_gpio(GPIO_NUM_17);                                                  
	gpio_set_direction(GPIO_NUM_17, GPIO_MODE_OUTPUT);
	gpio_set_level(GPIO_NUM_17, 1);                                                      


	//----------------------------------------------
	//--- create task for controlling the motors ---
	//----------------------------------------------
	//task that receives commands, handles ramp and current limit and executes commands using the motordriver function
	xTaskCreate(&task_motorctl, "task_motor-control", 2048, NULL, 6, NULL);

	//------------------------------
	//--- create task for buzzer ---
	//------------------------------
	xTaskCreate(&task_buzzer, "task_buzzer", 2048, NULL, 2, NULL);


	//-----------------------------------
	//--- create task for fan control ---
	//-----------------------------------
	//task that evaluates and processes the button input and runs the configured commands
	xTaskCreate(&task_fans, "task_fans", 2048, NULL, 1, NULL);


	//beep at startup
	buzzer.beep(3, 70, 50);
#endif



#ifndef BRAKE_TEST_ONLY
	//-------------------------------------------
	//--- create tasks for uart communication ---
	//-------------------------------------------
	uart_init();
	xTaskCreate(task_uartReceive, "task_uartReceive", 4096, NULL, 10, NULL);
	xTaskCreate(task_uartSend, "task_uartSend", 4096, NULL, 10, NULL);
#endif



#ifdef SPEED_SENSOR_TEST
	speedSensor_config_t speedRight_config{
		.gpioPin = GPIO_NUM_18,
			.degreePerGroup = 72,
			.tireCircumferenceMeter = 0.69,
			.directionInverted = false,
			.logName = "speedRight",
	};
	speedSensor speedRight (speedRight_config);
#endif


	//---------------------------
	//-------- main loop --------
	//---------------------------
	//does nothing except for testing things
	while(1){

#ifdef SPEED_SENSOR_TEST
		vTaskDelay(100 / portTICK_PERIOD_MS);
		//speedRight.getRpm();
		ESP_LOGI(TAG, "speedsensor-test: rpm=%fRPM, speed=%fkm/h dir=%d, pulseCount=%d, p1=%d, p2=%d, p3=%d lastEdgetime=%d", speedRight.getRpm(), speedRight.getKmph(), speedRight.direction, speedRight.pulseCounter, (int)speedRight.pulseDurations[0]/1000,  (int)speedRight.pulseDurations[1]/1000, (int)speedRight.pulseDurations[2]/1000,(int)speedRight.lastEdgeTime);
#endif
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

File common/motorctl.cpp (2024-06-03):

#include "motorctl.hpp"
#include "esp_log.h"
#include "types.hpp"

//tag for logging
static const char * TAG = "motor-control";

#define TIMEOUT_IDLE_WHEN_NO_COMMAND 15000 // turn motor off when still on and no new command received within that time
#define TIMEOUT_QUEUE_WHEN_AT_TARGET 5000  // time waited for new command when motors at target duty (e.g. IDLE) (no need to handle fading in fast loop)

//====================================
//========== motorctl task ===========
//====================================
//task for handling the motors (ramp, current limit, driver)
void task_motorctl( void * ptrControlledMotor ){
    //get pointer to controlledMotor instance from task parameter
    controlledMotor * motor = (controlledMotor *)ptrControlledMotor;
    ESP_LOGW(TAG, "Task-motorctl [%s]: starting handle loop...", motor->getName());
    while(1){
        motor->handle();
        vTaskDelay(20 / portTICK_PERIOD_MS);
    }
}



//=============================
//======== constructor ========
//=============================
//constructor, simultaniously initialize instance of motor driver 'motor' and current sensor 'cSensor' with provided config (see below lines after ':')
controlledMotor::controlledMotor(motorSetCommandFunc_t setCommandFunc,  motorctl_config_t config_control, nvs_handle_t * nvsHandle_f, speedSensor * speedSensor_f, controlledMotor ** otherMotor_f):
    //create current sensor
	cSensor(config_control.currentSensor_adc, config_control.currentSensor_ratedCurrent, config_control.currentSnapToZeroThreshold, config_control.currentInverted),
    configDefault(config_control){
		//copy parameters for controlling the motor
		config = config_control;
        log = config.loggingEnabled;
		//pointer to update motot dury method
		motorSetCommand = setCommandFunc;
        //pointer to nvs handle
        nvsHandle = nvsHandle_f;
        //pointer to other motor object
        ppOtherMotor = otherMotor_f;
        //pointer to speed sensor
        sSensor = speedSensor_f;

        //create queue, initialize config values
		init();
	}



//============================
//========== init ============
//============================
void controlledMotor::init(){
    commandQueue = xQueueCreate( 1, sizeof( struct motorCommand_t ) );
    if (commandQueue == NULL)
    ESP_LOGE(TAG, "Failed to create command-queue");
    else
    ESP_LOGI(TAG, "[%s] Initialized command-queue", config.name);

    // load config values from nvs, otherwise use default from config object
    loadAccelDuration();
    loadDecelDuration();

    // turn motor off initially
    motorSetCommand({motorstate_t::IDLE, 0.00});

    //cSensor.calibrateZeroAmpere(); //currently done in currentsensor constructor TODO do this regularly e.g. in idle?
}



//----------------
//----- fade -----
//----------------
//local function that fades a variable
//- increments a variable (pointer) by given value
//- sets to target if already closer than increment
//TODO this needs testing
void fade(float * dutyNow, float dutyTarget, float dutyIncrement){
    float dutyDelta = dutyTarget - *dutyNow; 
    if ( fabs(dutyDelta) > fabs(dutyIncrement) ) { //check if already close to target
        *dutyNow = *dutyNow + dutyIncrement;
    }
    //already closer to target than increment
    else {
        *dutyNow = dutyTarget;
    }
}



//----------------------------
//----- getStateFromDuty -----
//----------------------------
//local function that determines motor the direction from duty range -100 to 100
motorstate_t getStateFromDuty(float duty){
	if(duty > 0) return motorstate_t::FWD;
	if (duty < 0) return motorstate_t::REV;
	return motorstate_t::IDLE;
}



//==============================
//=========== handle ===========
//==============================
//function that controls the motor driver and handles fading/ramp, current limit and deadtime
void controlledMotor::handle(){

    //TODO: History: skip fading when motor was running fast recently / alternatively add rot-speed sensor

    //--- RECEIVE DATA FROM QUEUE ---
    if( xQueueReceive( commandQueue, &commandReceive, timeoutWaitForCommand / portTICK_PERIOD_MS ) ) //wait time is always 0 except when at target duty already
    {
        if(log) ESP_LOGV(TAG, "[%s] Read command from queue: state=%s, duty=%.2f", config.name, motorstateStr[(int)commandReceive.state], commandReceive.duty);
        state = commandReceive.state;
        dutyTarget = commandReceive.duty;
		receiveTimeout = false;
		timestamp_commandReceived = esp_log_timestamp();

    }





// ----- EXPERIMENTAL, DIFFERENT MODES -----
// define target duty differently depending on current contro-mode
//declare variables used inside switch
float ampereNow, ampereTarget, ampereDiff;
float speedDiff;
    switch (mode)
    {
    case motorControlMode_t::DUTY: // regulate to desired duty (as originally)
        //--- convert duty ---
        // define target duty (-100 to 100) from provided duty and motorstate
        // this value is more suitable for t
        // todo scale target input with DUTY-MAX here instead of in joysick cmd generationhe fading algorithm
        switch (commandReceive.state)
        {
        case motorstate_t::BRAKE:
            // update state
            state = motorstate_t::BRAKE;
            // dutyTarget = 0;
            dutyTarget = fabs(commandReceive.duty);
            break;
        case motorstate_t::IDLE:
            dutyTarget = 0;
            break;
        case motorstate_t::FWD:
            dutyTarget = fabs(commandReceive.duty);
            break;
        case motorstate_t::REV:
            dutyTarget = -fabs(commandReceive.duty);
            break;
        }
        break;
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

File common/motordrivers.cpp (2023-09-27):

#include "motordrivers.hpp"
#include "esp_log.h"
#include "types.hpp"

//TODO: move from ledc to mcpwm?
//https://docs.espressif.com/projects/esp-idf/en/v4.3/esp32/api-reference/peripherals/mcpwm.html#
//https://github.com/espressif/esp-idf/tree/v4.3/examples/peripherals/mcpwm/mcpwm_basic_config

//Note fade functionality provided by LEDC would be very useful but unfortunately is not usable here because:
//"Due to hardware limitations, there is no way to stop a fade before it reaches its target duty."

//tag for logging
static const char * TAG = "motordriver";

//ms to wait in IDLE before BRAKE until relay actually switched
#define BRAKE_RELAY_DELAY_MS 300


//====================================
//===== single100a motor driver ======
//====================================

//-----------------------------
//-------- constructor --------
//-----------------------------
//copy provided struct with all configuration and run init function
single100a::single100a(single100a_config_t config_f){
	config = config_f;
	init();
}



//----------------------------
//---------- init ------------
//----------------------------
//function to initialize pwm output, gpio pins and calculate maxDuty
void single100a::init(){

	//--- configure ledc timer ---
	ledc_timer_config_t ledc_timer;
	ledc_timer.speed_mode       = LEDC_HIGH_SPEED_MODE;
	ledc_timer.timer_num        = config.ledc_timer;
	ledc_timer.duty_resolution  = config.resolution; //13bit gives max 5khz freq
	ledc_timer.freq_hz          = config.pwmFreq;
	ledc_timer.clk_cfg          = LEDC_AUTO_CLK;
	//apply configuration
	ledc_timer_config(&ledc_timer);

	//--- configure ledc channel ---
	ledc_channel_config_t ledc_channel;
	ledc_channel.channel    = config.ledc_channel;
	ledc_channel.duty       = 0;
	ledc_channel.gpio_num   = config.gpio_pwm;
	ledc_channel.speed_mode = LEDC_HIGH_SPEED_MODE;
	ledc_channel.hpoint     = 0;
	ledc_channel.timer_sel  = config.ledc_timer;
	ledc_channel.intr_type = LEDC_INTR_DISABLE;
	ledc_channel.flags.output_invert = 0; //TODO: add config option to invert the pwm output?
										  //apply configuration
	ledc_channel_config(&ledc_channel);

	//--- define gpio pins as outputs ---
	gpio_pad_select_gpio(config.gpio_a);
	gpio_set_direction(config.gpio_a, GPIO_MODE_OUTPUT);
	gpio_pad_select_gpio(config.gpio_b);
	gpio_set_direction(config.gpio_b, GPIO_MODE_OUTPUT);
	gpio_pad_select_gpio(config.gpio_brakeRelay);
	gpio_set_direction(config.gpio_brakeRelay, GPIO_MODE_OUTPUT);

	//--- calculate max duty according to selected resolution ---
	dutyMax = pow(2, ledc_timer.duty_resolution) -1;
	ESP_LOGW(TAG, "initialized single100a driver");
	ESP_LOGW(TAG, "resolution=%dbit, dutyMax value=%d, resolution=%.4f %%", ledc_timer.duty_resolution, dutyMax, 100/(float)dutyMax);
}



//---------------------------
//----------- set -----------
//---------------------------
//function to put the h-bridge module in the desired state and duty cycle
void single100a::set(motorCommand_t cmd){
	set(cmd.state, cmd.duty);
}

void single100a::set(motorstate_t state_f, float duty_f){

	//scale provided target duty in percent to available resolution for ledc
	uint32_t dutyScaled;
	if (duty_f > 100) { //target duty above 100%
		dutyScaled = dutyMax;
	} else if (duty_f < 0) { //target at or below 0%
		state_f = motorstate_t::IDLE;
		dutyScaled = 0;
	} else { //target duty 0-100%
			 //scale duty to available resolution
		dutyScaled = duty_f / 100 * dutyMax;
	}

	ESP_LOGV(TAG, "target-state=%s, duty=%d/%d, duty_input=%.3f%%", motorstateStr[(int)state_f], dutyScaled, dutyMax, duty_f);

	//TODO: only when previous mode was BRAKE?
	if (state_f != motorstate_t::BRAKE){
		//reset brake wait state
		brakeWaitingForRelay = false;
		//turn of brake relay
		gpio_set_level(config.gpio_brakeRelay, 0);
	}

	//put the single100a h-bridge module in the desired state update duty-cycle
	//TODO maybe outsource mode code from once switch case? e.g. idle() brake()...
	switch (state_f){
		case motorstate_t::IDLE:
			ledc_set_duty(LEDC_HIGH_SPEED_MODE, config.ledc_channel, dutyScaled); 
			ledc_update_duty(LEDC_HIGH_SPEED_MODE, config.ledc_channel);
			//TODO: to fix bugged state of h-bridge module when idle and start again, maybe try to leave pwm signal on for some time before updating a/b pins?
			//no brake: (freewheel)
			//gpio_set_level(config.gpio_a, config.aEnabledPinState);
			//gpio_set_level(config.gpio_b, !config.bEnabledPinState);
			gpio_set_level(config.gpio_a, config.aEnabledPinState);
			gpio_set_level(config.gpio_b, config.bEnabledPinState);
			break;
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

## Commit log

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2022-06-08 Create class 'evaluatedJoystick'
    - Create class 'evaluatedJoystick'
    - evaluates a joystick with 2 analog signals
    - scales the adc input to coordinates with detailed tolerances
    - calculates angle and radius
    - defines an enum with position information
    - Add joystick configuration and class instance to config.cpp
    - Add code for testing the new class to main.cpp
    - Add joystick.cpp to cmakelists
    now function `joystick.getData` can be used globally to obtain a struct with
    current position data of the joystick
    [config.cpp, joystick.cpp, main.cpp]
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2022-06-10 Add 'buzzer.hpp, buzzer.cpp' Add instance 'button'
    - Copy buzzer function from gate project
    this makes it possible to easily trigger and queue up buzzing events
    without having to worry about delaying the program
    - Add instance buzzer to config
    - Add code for testing the buzzer to main.cpp
    [buzzer.cpp, config.cpp, main.cpp]
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2022-06-17 Utilize SPIFFS for serving the app with web-server
    With this commit the webserver of the controller can serve a folder (/react-app/build/), when the ip is accessed in a web-browser.
    Currently the react app is successfully served and the armchair can be controlled when in HTTP mode and connected via AP.
    - CMakeLists: Add command that creates and flashes the spiffs partition when running
    idf.py flash
    - main.cpp: Add function to initialize spiffs
    - http.cpp: uncomment handler for default URL (accesses spiffs)
    - Add partitions.csv: needed for the creation of spiffs.bin during
    compilation
    - Add sdkconfig: It was necessary to change the FLASH_SIZE from 2MB to
    4MB. To avoid having the same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
    [partitions.csv]
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2022-06-19 Change dutyMax and fade, Add reboot cmd (1x press)
    decrease ramp from 3000ms to 900ms (as in old project)
    increase max duty from testing 60 to 94
    Add reboot command (untested)
    [button.cpp, config.cpp, joystick.cpp]
2022-06-19 Move coordinate scaling from app to controller
    - joystick.cpp/hpp:
    - move method scaleCoordinate from joystick class to public function
    - modify scaleCoordinate function to accept float values instead of
    ADC pin, change tolerance parameters to percent instead of absolute
    number
    - change method getData to use the public function now
    - control.cpp:
    - use scaleCoordinate function in http mode
    - calculate radius in http mode
    - config.cpp
    - adjust tolerance thresholds for joystick to percent
    - App.js
    - disable "snap to zero" feature -> just scale joystick output to
    value of -1 to 1
    [config.cpp, control.cpp, joystick.cpp]
2022-06-20 Add timeout feature to control
    Add feature that switches to mode IDLE when duty of both motors did not
    change over certain time.
    control.cpp/hpp:
    - add private function that handles timeout
    - add public function that resets timeout
    - add slow loop with timeout handle inside control handle loop
    [control.cpp]
2022-06-21 Move config parameters from control to config
    - create new struct control_config_t with several variables previously
    hardcoded in control.cpp
    - modified constructor: add config parameter
    - add definition of config struct in config.cpp
    typedef struct control_config_t {
    controlMode_t defaultMode; //default mode after startup and toggling IDLE
    //--- timeout ---
    uint32_t timeoutMs; //time of inactivity after which the mode gets switched to IDLE
    float timeoutTolerancePer; //percentage the duty can vary between timeout checks considered still inactive
    //--- http mode ---
    float http_toleranceZeroPer;//percentage around joystick axis the coordinate snaps to 0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
    [config.cpp, control.cpp]
2022-06-22 Fix bug in scaling, Fix http cmd gen, Fix overflow
    Fix several bugs noticed while testing the preceding commits in dev
    branch:
    - Fix bug in function scaleCoordinate
    - scaling was wrong resulting in negative/inverted values at start of axis
    - Adjust timeout value from 30s to 5min
    - Fix http joystick behaivor
    - calculate angle, radius and evaluate position AFTER the coordinates
    have been scaled in control.cpp (bug introduced when switching applying tolerance
    on controller instead of in the app)
    - Add independent toleranceZero for X and Y axis -> unnecessary to have
    large tolerance for x axis... makes turning more sensitive
    - Fix stack overflow in control task
    - controller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
    [config.cpp, control.cpp, http.cpp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]
2022-06-24 Add different tolerances for X and Y coordinate
    As already did for http joystick:
    - Add different config options tolerance zero for X and Y axis for
    normal/actual joystick.
    This makes it possible to set Y tolerance to a lower value resulting in
    a more responsive turning action, with still having a large range around
    X axis for turning mode
    [config.cpp, joystick.cpp]
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2022-07-05 Add exponential scaling of stick coordinates
    - joystick.hpp/cpp
    - add function joystick_scaleCoordinatesExp(joystickData_t * data, float exponent)
    which updates joystick data with its scaled coordinates and
    re-calculated radius
    - control.cpp
    - scale coordinates exponential (pow 2) in JOYSTICK mode
    - scale coordinates exponential (pow 2) in HTTP mode
    - fixed swapped x/y zero tolerances for hardware joystick
    Note: tested armchair with scaling exponents 1.5; 2; 3 and noticed that
    2 works best
    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
    [config.cpp, control.cpp, joystick.cpp]
2022-07-06 Add linear scaling of stick coordinates
    - add function joystick_scaleCoordinatesLinear(joystickData_t * data, float pointX, float pointY)
    that scales the coordinates with 2 different slopes before and
    after certain point
    - scale coordinates linear with new function instead of exponential in JOYSTICK mode
    - scale coordinates linear with new function instead of exponential in HTTP mode
    - adjust / decrease http joystick tolerances
    Note: tested the armchair in http and joystick mode briefly and
    optimized the scaling point slightly
    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
    [config.cpp, control.cpp, joystick.cpp]
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2022-07-14 Revert "Add hysteresis to joystick position X-Axis"
    While testing this feature briefly that approach did not appear to be a good idea.
    - noticed that the driving with joystick was a little unintuitive/unexpected (maybe just not used to it?)
    - BUG that the state does not reset to center when previous state was
    X-AXIS? Resulting in the armchair to slightly shake randomly at
    joystick center
    -> this has to be fixed if this approach is tested again.
    This reverts commit b2b12fe5de1e16ea2f25dfa4b0c3ac6845024c71.
    [http.cpp, joystick.cpp]
2022-07-16 Add fade-down functionality to motorctl (bug)
    With this changes the motors are faded down (same as already existing fading up)
    when the target duty suddenly decreases.
    It can be configured or disabled with setting msFadeDown to 0 in config struct of
    motorctl object.
    - Add new config parameter msFadeDown
    - Change msFade to msFadeDown
    - Add fade down functionality to motorctl instead of just setting the
    duty to lower value
    !!!TODO: fix major BUG when motor direction changes suddenly (before fade got to
    0) the motor immediately starts in other direction with previous duty
    (no/less fading up happening)
    [config.cpp, motorctl.cpp, motorctl.hpp]
2022-07-17 Change motorctl.handle from STATE to duty -100-100
    For fading-down and delay-between-state-change to work correctly when switching between motorstates
    (e.g. FWD -> REV) the handle function was changed.
    using a duty value -100 for reverse 100% and +100 for forward 100%
    allows are more mathematical approach
    changes to motorctl.cpp:
    - convert state and duty to duty -100 to 100 when receiving target
    command at start
    - convert duty -100-100 back to state and duty at the end for applying
    motor commands
    [motorctl.cpp]
2022-07-17 Fix bug no fwd downfade; Add BRAKE; cleanup; [bug]
    - Fix bug where downfade did not work when driving forward
    - Add BRAKE command functionality to motorctl (untested, since not used anywhere atm)
    - Cleanup: Optimize code, add comments
    !!!TODO: there is a fault in the current concept/logic:
    fading up/down generally works, however when accelerating
    REVERSE fade-down is utilized instead of fade-up.
    => Fix that bug, fade down should only be used when decelerating.
    [config.cpp, motorctl.cpp]
2022-07-18 Fix fading: correctly use different accel, decel ramps
    - Change fading algorithm to handle Acceleration and Deceleration for
    forward and reverse separately (4 different cases)
    - rename variables to make fading direction more obvious
    e.g. msFadeUp -> msFadeAccel or dutyIncrementDon -> dutyIncrementDecel
    TODO: fading needs optimization
    [config.cpp, motorctl.cpp, motorctl.hpp]
2022-07-23 Fix bug: fade stuck at zero; Adjust fade durations
    - Fix bug where case duty=0 was not handled in fading if structure thus no
    incrementing action happened anymore (stuck at duty = 0)
    - Set fade duration (acceleration, deceleration) to realistic value in
    config
    [config.cpp, motorctl.cpp]
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2022-07-24 Add functions to send button-event to control task
    - control.cpp: - Add method sendButtonEvent to control class
    - joystick mode: define joystick center at button event
    - massage mode: toggle freezing of joystick input at
    button event
    - button.cpp: remove reboot command (1x press)
    - button.cpp: add command sendButtonEvent to control task (1x press)
    [button.cpp, control.cpp]
2022-07-24 Modify fading when switching from/to MASSAGE mode
    In massage mode it is required that the motors react quicker, Added the
    following functionality to control.cpp:
    - when changing to MASSAGE mode the downfading is disabled and upfading is
    reduced
    - when changing from MASSAGE mode downfading is enabled and upfading reset
    to default value
    [control.cpp]
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2022-07-25 Fix Bug unexpected movement MASSAGE; Adjustments
    Fix bug where armchair moved too long every once in a while (especially
    at start).
    Minor adjustments of parameters.
    main.cpp:
    - set individual task priorities for each task e.g. fan or buzzer task has very low priority (did not have any immediate effect though while testing)
    - increase handle interval of motorctl
    change from 20 to 10 (same frequency as generation of massage
    commands)
    -> this fixed the bug with unexpected movement (motorctl could not
    process every command from massage mode)
    control.cpp:
    - decrease delay in massage mode for more detail/levels at joystick
    radius (from 20 to 10ms)
    - increase fading in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
    [control.cpp, joystick.cpp, main.cpp]
2022-07-25 Add button commands; Update Readme
    button.cpp:
    - Add command: reboot when long button press
    - Add command: switch to mode JOYSTICK with 3x press
    Readme:
    - rework table with switch functions
    - add new commands to table
    - add drink holder to planned features
    joystick.cpp:
    - fix bug: missing 'break;' for switch case in function joystick_CommandsShaking
    [button.cpp, joystick.cpp]
2022-07-26 Add button cmd x12: alternative joystick mapping
    New command and feature also made some general changes to control and button necessary
    - add optional parameter to joystick_CommandsDriving function
    bool altStickMapping (default false)
    if true this currently swaps BOTTOM_LEFT with BOTTOM_RIGHT for experimental
    different joystick mapping
    - fix/move variable declaration outside of switch
    - add 12x case: send count to control task
    - create new section in handle loop for button events
    - move x1 commands from JOYSTICK and MASSAGE case to new button
    section
    - remove unnecessary variable buttonEvent (only using buttonCount now)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
    [button.cpp, control.cpp, joystick.cpp]
2022-07-28 Fix bug: massage stick freeze not resetting
    When switching mode from MASSAGE to other mode while joystick input
    frozen (button). It was still frozen when switching back to MASSAGE mode
    later. This is confusing and is seen as a bug
    -> reset locked input variable to false on mode change
    [control.cpp]
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2022-08-11 Fix stack overflow, apply and restore fading [functional]
    auto.cpp:
    apply fadeAccel and fadeDecel from commands to motors
    double stack size of button task (crashed controller every time)
    Modify test command to actually eject armchair leg support
    apply generated motor commands to motors
    rename some variables:
    typo: fadeAccel
    more specific: auto_instruction_t
    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
    [auto.cpp, button.cpp, control.cpp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]
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2022-08-11 Add longPressed case to button class, rework cmds
    - slightly decrease msFadeDecel by 100ms
    - different approach in button.cpp for case last button press was long
    e.g. reworked commands:
    - 1x long press = restart
    - 1x short press = center stick, freeze
    - 1x short 1x long = run new auto commands
    - 2x short = toggle idle
    - change default minOnMs / minOffMs for evaulated switch class -> fix
    button presses sometimes not recognized
    [button.cpp, config.cpp]
2023-05-27 Update joystick config, Add option JOYSTICK_LOG_IN_IDLE
    - add more debug output in joystick getData function
    - update joystick config with new min/max values while testing
    => fixed bugged movement (joystick unusable) after winter
    - bump esp-idf version since successfully compiled with 4.4.4
    [config.cpp, control.cpp, joystick.cpp]
2023-08-13 Config: Replace abInverted with a- and bEnabledPinState
    Changed config and code for motor driver:
    Now its possible to configure whether a and b pins are inverted separately
    e.g. a connected to mosfets (inverted) and b connected directly
    [config.cpp, motordrivers.cpp]
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2023-08-14 Update config with new pin assignment
    - apply changed pins to config (according to new hardware configuration)
    - calibrate joystick, more tolerance
    [config.cpp]
2023-08-15 Rework fan control: single pin, more delay, config
    - remove second fan instance since both fans are controlled via one pin
    now
    - more config options so fans turn on less at short movements
    => less noise and less relay cycles
    [config.cpp, fan.cpp, main.cpp]
2023-08-15 Adjust config: more fade, stick tolerance, less startDuty
    turned out that higher voltage of new battery results in way more
    responsive motors.
    Adjust this with available settings (less shaking)
    [config.cpp, joystick.cpp]
2023-08-16 Fix bugged coordinate/radius scaling
    - uncomment coordinate scaling which caused unwanted behaivor
    especially that radius never got to 1 when joystick diagonal
    resulting in loss of power/speed in curves
    - now scaling radius only which is the desired functionality
    - optimize debug logging
    - fix joystick calibration config (invertion was mistaken)
    [config.cpp, joystick.cpp]
2023-08-21 Optimize turning: allow duty=0 for inner wheel, prepare ratio snap threshold
    - joystick command generation:
    - also remove min duty offset with changing ratio
    - prepare threshold where ratio snaps to max for easier turning
    -> issue with driver has to be fixed first
    - minor motordriver optimization / add commented out debug mode
    (driver forward in idle)
    [joystick.cpp, motordrivers.cpp]
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2023-08-22 Cleanup: comments, structure, warnings
    went trough all current files:
    - remove old comments
    - change structure / newlines
    - main.cpp: outsource loglevel function
    - http.cpp: FIX compiler warnings
    currentsensor.hpp
    [config.cpp, control.cpp, fan.cpp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]
2023-08-22 Add deadTime support (time off between dir change)
    add config option for minimum time motor has to be in IDLE before
    changing direction. Try to prevent drivers from obvious extreme
    overload. At least prevent full speed switch
    Untested but simulated via log output
    [config.cpp, motorctl.cpp, motorctl.hpp]
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2023-08-30 Fix broken http mode (crash at init)
    revert changes from previous commit
    [http.cpp]
2023-08-30 2 boards: split code, outsource common, remove duplicate files
    - outsoruce common files and separate common types from source files (new
    common/types.hpp)
    - split source files to 2 board folders (relevant only, no duplicate)
    - currently boards compile successfull but not functional at all
    - comment out currently incompatible code
    [partitions.csv]
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2023-08-30 Fix broken http mode (crash at init)
    revert changes from previous commit in dev
    [http.cpp]
2023-08-30 send, receive, apply motorCommands works (proof of concept); add timeout
    - board_control successfully sends motor commands to board_motorctl
    - board_motorctl receives and applies motor commands
    note: control pcb currently switches to HTTP mode after startup for testing
    with data from ui
    - partially commented in code that has to be reworked
    - control: send commands via uart instead of to motor objects
    - board motorctl handled motor: add timeout when no target data
    received (e.g. control pcb offline / uart bugged)
    - board motorctl uart: receive motorCommands_t struct and apply data to
    target state of handled motors
    - types: fix issue with global motorstateStr variable
    [config.cpp, control.cpp, main.cpp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]
2023-08-30 Add message framing (start, end, escape bytes) to UART
    Same functionality as previous commit. But way more stable and clean.
    Previous proof of concept approach had issues with random partial or
    too large messages due to time based method
    Rework send and receive functions to work more stable
    - send: encode data with frame (start, end byte)
    - receive: read each byte one after the other, assemble message,
    handle actual data in handle function
    - add semaphore to write operation to prevent parallel write of
    different data when called from other tasks
    [main.cpp, uart.cpp, uart_common.cpp]
2023-08-30 Control: Rework timeout to work standalone (untested)
    rework and enable timeout feature to work independent of handledmotor
    object now uses generated commands instead of acutal motor duty
    not testet yet
    [control.cpp]
2023-08-30 Control: Rework button functionality - standalone
    - re-enable button functionality
    - make button independent of controlledmotor objects
    - disable 2x eject support command
    - disable 8x toggle fading command
    [button.cpp, main.cpp]
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2023-09-04 Add brake-relay support to motordriver
    [untested]
    Turn on brake relays in BRAKE state
    Also wait certain time for relays to switch before shorting the driver
    Add config option for brake relay pin
    Initialize pin in constructor
    [config.cpp, motordrivers.cpp]
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2023-09-05 Fix Bug brake not working at all
    BRAKE state was not possible with previous state
    now IDLE is not forced when duty 0
    Also adjust some logging
    [main.cpp, motorctl.cpp, motordrivers.cpp]
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2023-09-07 Revert to V2.0 single board (additional folder)
    New controller will be run with single controller at first...
    get single board version from V2.0 and create new folder
    (two boards version is kept)
    -> copied firmware from e6e586e5855d81ee726bb9a0fbe8ab12def5eeef
    [partitions.csv]
2023-09-07 Outsource currentsensor, motorctl, motordrivers to common/
    since board_single uses mostly the same code as board_control and
    board_motorctl several files are outsorced to common folder to prevent
    dupliate code and different versions
    [buzzer.cpp, currentsensor.cpp, motorctl.cpp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]
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2023-09-09 Fix stack-overflow, Adjust logging, test-ready
    enable all tasks in main for full function test with new driver
    [main.cpp, motorctl.cpp, motordrivers.cpp]
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2023-09-11 Hotfix: swap joystick X/Y pins, log 5V regulator start
    jsut re-wired the pcb.
    apparently joystick was wired wrong previously
    [config.cpp, main.cpp]
2023-09-12 Rework display: separate task, add battery percent
    slightly rework hacked display test
    - new code structure
    - split code in several functions
    - add task for display instead of running it in main()
    - functions to convert voltage to battery percent charged
    - show percentage and voltage on display
    [display.cpp, main.cpp]
2023-09-12 Outsource speedsensor, Display: show speed
    - move speedsensor files from motorctl pcb to common
    - single pcb create and configure global speedsensor objects
    - display: create fast slow veryslow loop
    - clear display every 30s
    - show speed in rpm and km/h
    NOTE: speedsensor needs fix, direction unreliable
    [config.cpp, display.cpp, speedsensor.cpp]
2023-09-13 Sabertooth: Add uart-mutex; Add both-off serial command
    - add mutex around mutex send instruction
    - add minimum delay between sent messages
    - detect situation where both motors are off and send special both motor
    stop command. This might fix issue "right motor stay always on"
    [motordrivers.cpp]
2023-09-13 Fix bug right motor always on; Optimize comments
    Bug was fixed in previous commit already
    Only changed code slightly (better readable) work with duty instead of data
    Optimize comments in motordriver
    [motordrivers.cpp]
2023-09-13 Patch V2.1-board-motorctl to work with new common code
    Changes to outsourced motorctl code made configuration
    of currently unused board-motorctl from V2.1 incompatible
    -> patch config
    [config.cpp]
2023-09-27 Fix regular Crash (stack overflow display task)
    Fix regular crash caused by display task
    [main.cpp]
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2023-10-08 Add control mode 'ADJUST_CHAIR' (btn 1 short, 1 long)
    Add functional mode to control chair position via joystick
    Switch to that mode using button 1x short 1x long (prev eject support)
    [button.cpp, control.cpp]
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2024-02-11 Rework/simplify chairAdjust - now using a class
    - complete rework of chairAdjust.cpp/.hpp
    created a class cControlledRest which is more readable
    and saves a lot of duplicate code
    - joystick.cpp: move chair control via joystick to
    chairAdjust.cpp (prevents dependency loop)
    - button.cpp: fix bug instant idle when changing to ADJUST_CHAIR
    Note: briefly tested this state on a breakout board:
    Mode change and call of new class methods works.
    [button.cpp, chairAdjust.cpp, config.cpp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]
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2024-02-14 Integrate menu into control, Rework prev. button menu
    Armchair functions as before (all tasks enabled).
    Note: probably wrong encoder pin set in encoder.hpp
    Old button menu works as usual (opimized code).
    You can switch to new MENU state with 1x long press
    and exit the menu with 1x long press
    button.cpp: - use encoder queue instead of evaluated switch
    - simplify code, rework actions
    control.cpp: Add MENU state/mode
    -> control task: turns motors off and idles
    -> button task idles (button menu disabled)
    -> display task switches state to handle menu
    control.cpp: Optimize structure:
    Add methods to freeze stick and toggle stick mappin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
    [button.cpp, control.cpp, display.cpp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]
2024-02-14 Add functional menu items (accel/decel), Add menu-timeout
    menu.cpp:
    - add item center-Joystick (functional)
    - add item accel-Limit (functional)
    - add item decel-Limit (functional)
    - fix display freeze on timeout
    - add menu timeout
    - switch to previous mode on exit instead of always idle
    motorctl.cpp:
    - add getFade method, to get currently configured values
    - add log output on fade change
    [button.cpp, motorctl.cpp, motorctl.hpp]
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
